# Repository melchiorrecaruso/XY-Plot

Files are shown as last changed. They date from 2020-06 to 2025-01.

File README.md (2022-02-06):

# **XY-Plot**

A plotter is a printer designed for printing vector graphics. Instead of printing individual dots on the paper, plotters draw continuous lines.
This makes plotters ideal for printing architectural blueprints, engineering designs, and other CAD drawings. 

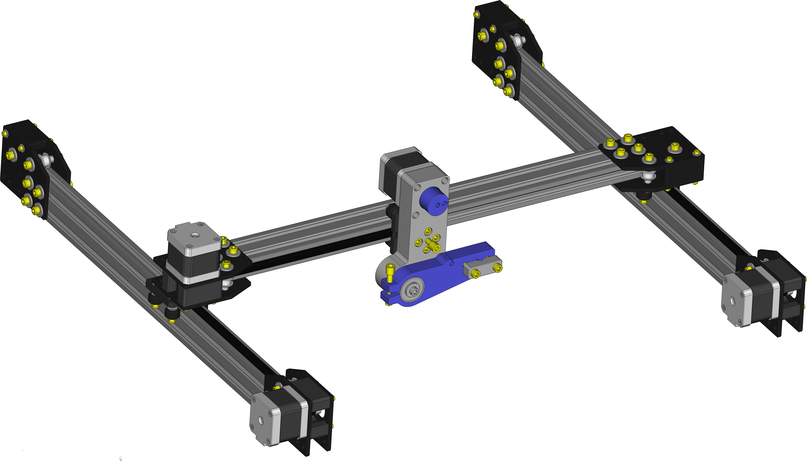
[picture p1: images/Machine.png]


## **XY-Plot hardware requirements**

The main components are:

>-  1x Arduino Uno R3 board or Mega 2560 R3;
>-  1x CNC Shield V3 expansion board;
>-  4x DRV8825 stepper motor driver;
>-  4x Stepper motor Nema-17 (min torque 40 Ncm);
>-  3x Timing belt pulley GT2 20T 5mmn bore;
>- 12x Smooth idler pulley with bearings GT2 20T 5mm bore;
>- 10m GT2 timming belt;
>-  1x 12V/5A power supplier;
>-  1x 3D-Printer for printing all hardware parts;
>-  40x40 beams, carriages. See [OpenBuilds parts store](https://openbuildspartstore.com/);
>-  Washers, bolts and nuts.

### **X Linear Actuator**
Prints parts and assembly two X axis linear actuator.

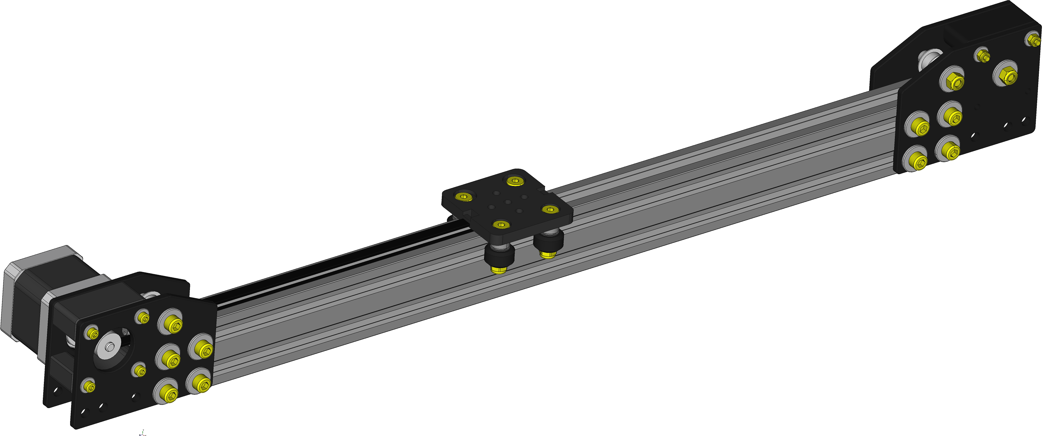
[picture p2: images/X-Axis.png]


### **Y Linear Actuator & Pen Holder**
Prints parts, assembly one Y axis linear actuator and pen holder.

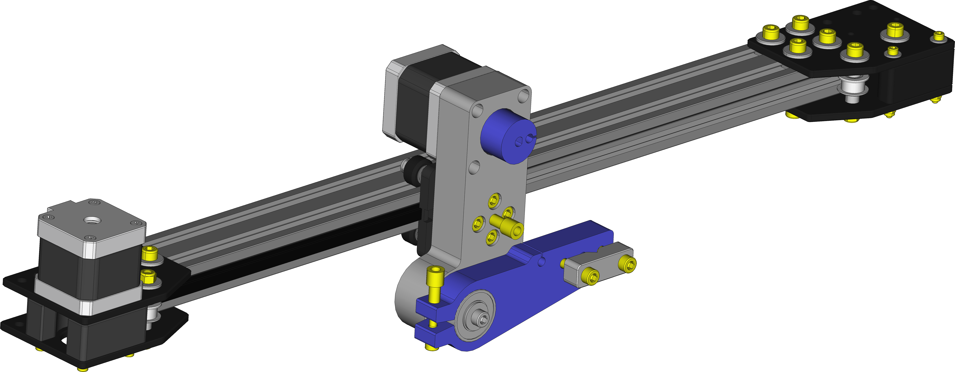
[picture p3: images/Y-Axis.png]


## **XY-Plot software requirements**

For compiling XY-Plot Client use [Lazarus IDE and FreePascal compiler](https://www.lazarus-ide.org/index.php?page=downloads).

**Libraries**:

>- [BGRA Controls Library](https://bgrabitmap.github.io/)
>- [LNet Library](https://lnet.wordpress.com/)

Use integrated [Online Package Manager](https://wiki.freepascal.org/Online_Package_Manager ) for installing all libraries.

**Build Client**:

```console
lazbuild --build-mode=Release xyplot.lpi
lazbuild --build-mode=Debug xyplot.lpi
```

**Build Server**:

For building and loading server sketch on Arduino board use [Arduino IDE](https://www.arduino.cc/en/Main/Software).

## **Before assembling**

Set the Vref current on DRV8825 stepper drivers. See the guide

>- [How to control a stepper motor with DRV8825](https://www.makerguides.com/drv8825-stepper-motor-driver-arduino-tutorial/)

## **Connecting to Arduino**

Nema 17 motors have 200 steps for rotation but by enabling microsteps on the Pololu drivers we can obtain up to 3200 steps for rotation which allows for much more precision. For doing that add four jumpers on green pins. 

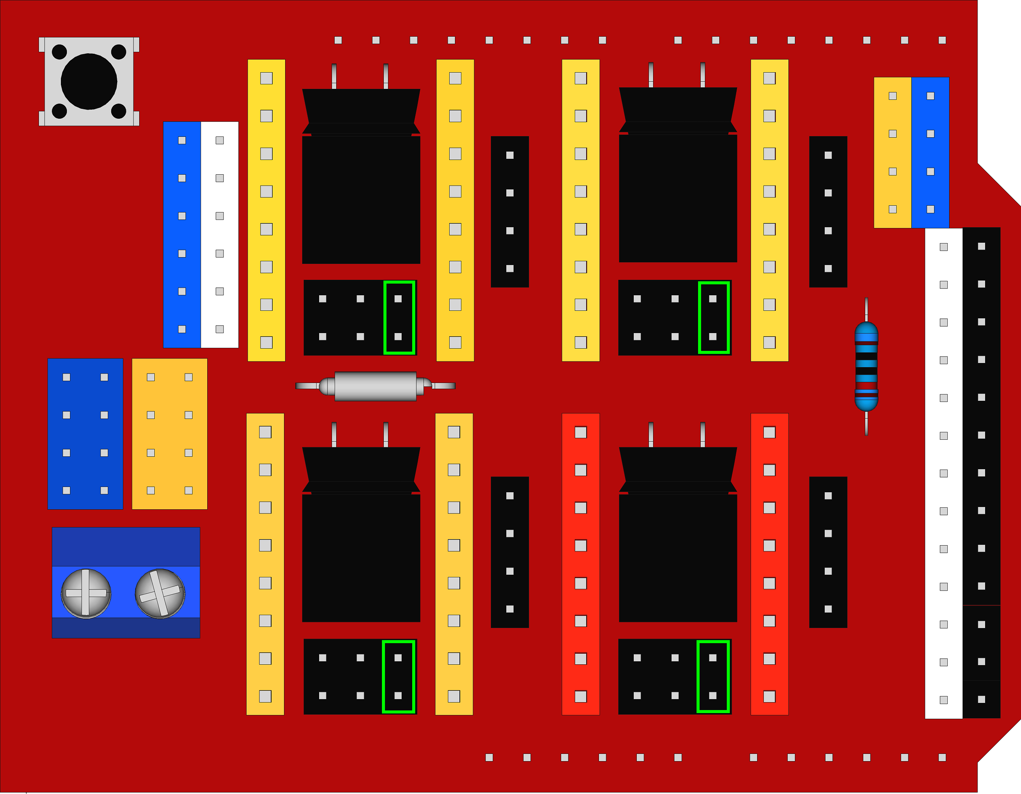
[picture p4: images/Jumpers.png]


**Then**
- Mount the stepper drivers on CNC schield board;
- Apply two jumpers on green pins for clonig X axis;
- Connect X motors to the blue pins;
- Connect Y motor to red pins;
- Connect Z motor to yellow pins.

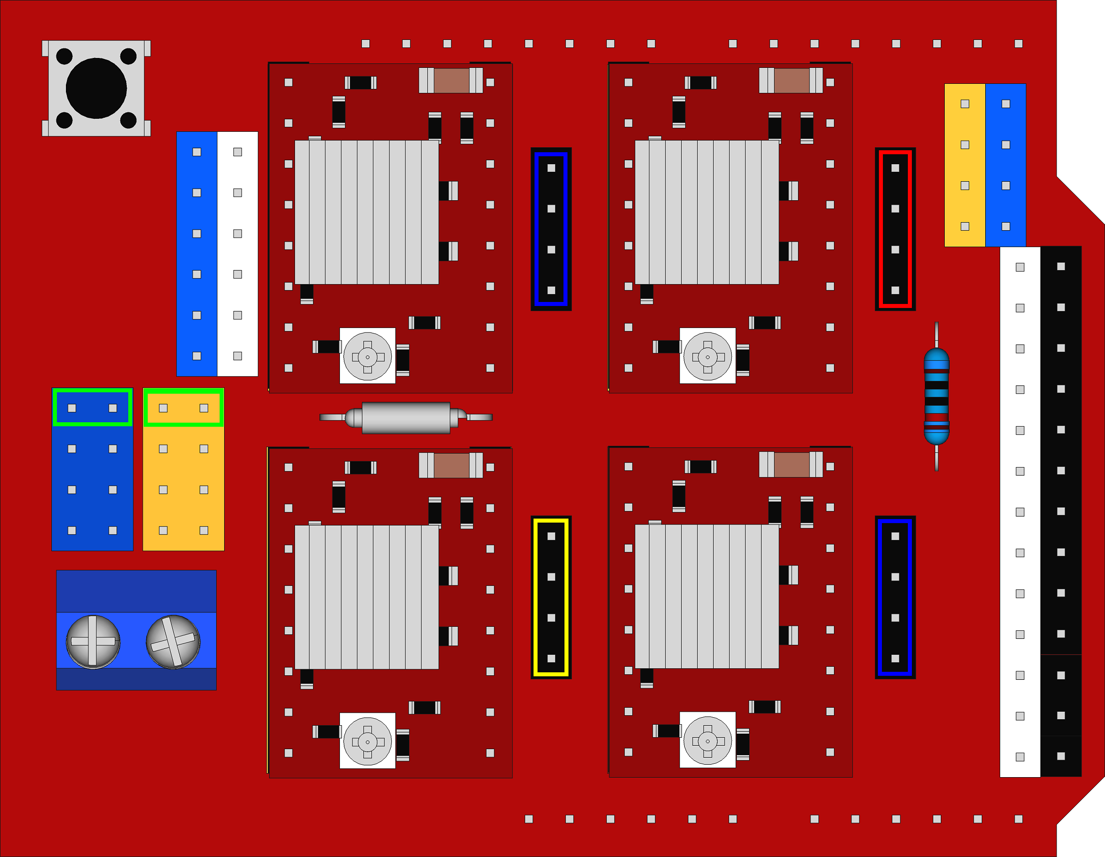
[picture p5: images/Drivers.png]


**Then**
- Mount CNC Shield on arduino board;
- Connect Arduino board to PC by usb port;
- Connect 12V power supply to CNC schield.

## **Starting**

Open XY-Plot client for connecting and controlling Plotter.

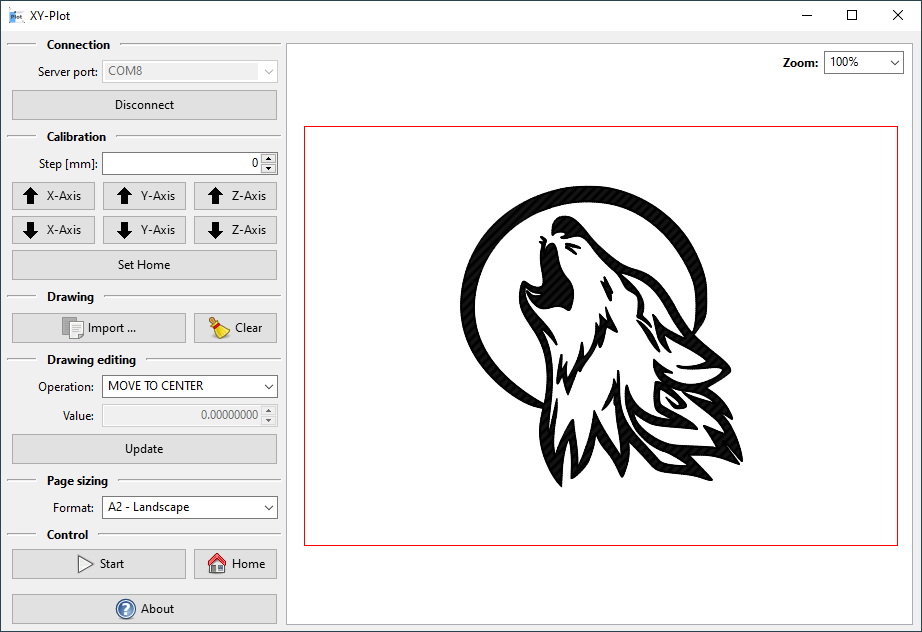
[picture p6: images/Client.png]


## **Boards Box**

Below a boards box example.

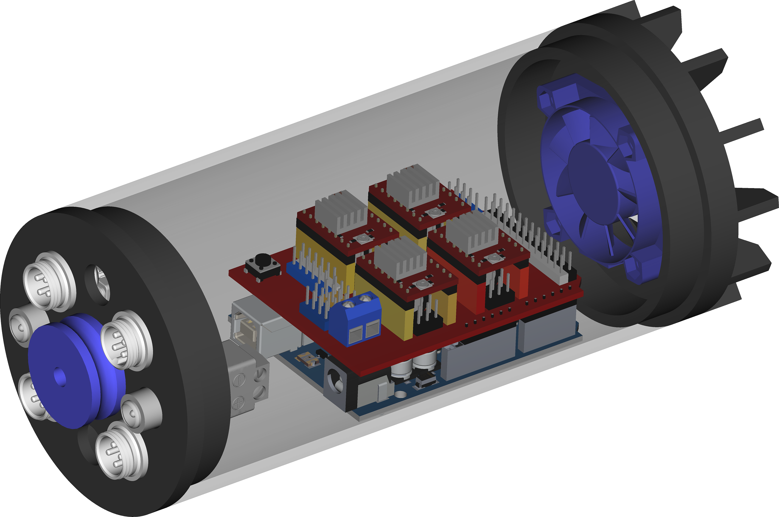
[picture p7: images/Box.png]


## **LICENSE**
[GNU General Public License v3.0](LICENSE)

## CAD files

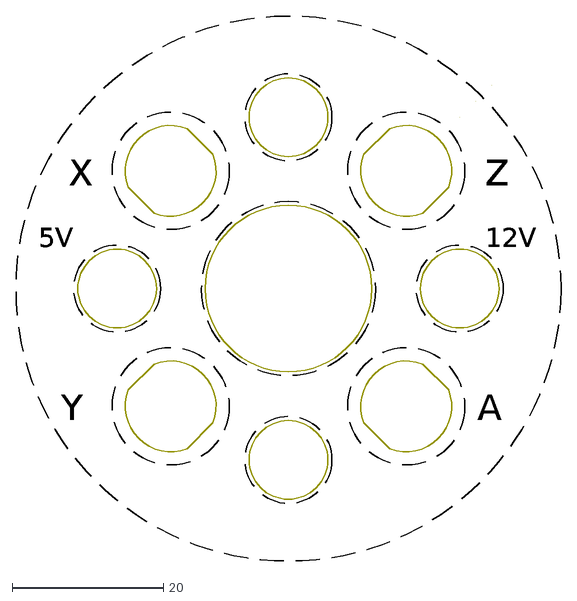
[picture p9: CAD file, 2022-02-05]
hardware/Decal/decal.dxf
X
Y
A
Z
12V
5V

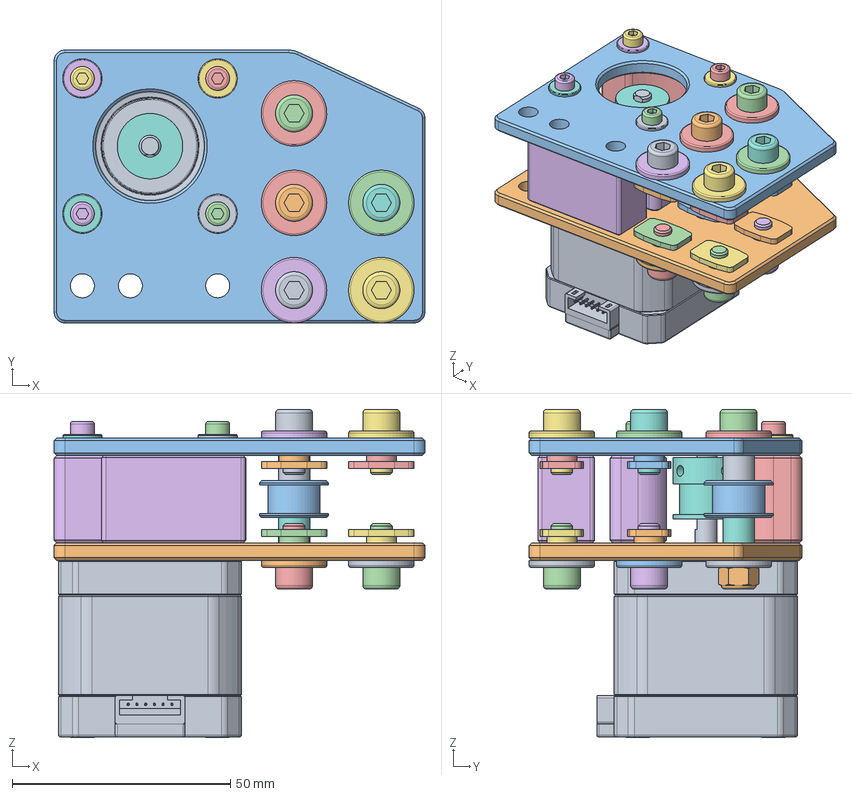
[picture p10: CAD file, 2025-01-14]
hardware/xyp1102.FCStd
85.0 x 62.5 x 75.3 mm
xyp1014_002
xyp1012_001
xyp1012_002
xyp1016_001
xyp1016_002
xyp1016_003
xyp1016_004
xyp1017_001
xyp1017_002
xyp1017_003
xyp1017_004
xyp1017_005
xyp1017_006
xyp1017_007
xyp1017_008
xyp1016_007
xyp1016_008
xyp1016_009
xyp1016_010
xyp1019_001
xyp1019_002
xyp1019_003
xyp1019_004
xyp1020_001
xyp1016_012
xyp1010_002
xyp1022_001
xyp1018_003
xyp1016_013
xyp1026_001
xyp1027_001
xyp1046_001
xyp1046_002
xyp1027_002
xyp1027_003
xyp1027_004
xyp1026_002
xyp1029_001
xyp1029_002
xyp1029_003
xyp1029_004
xyp1027_005
xyp1027_006
xyp1027_007
xyp1027_008
xyp1009_001

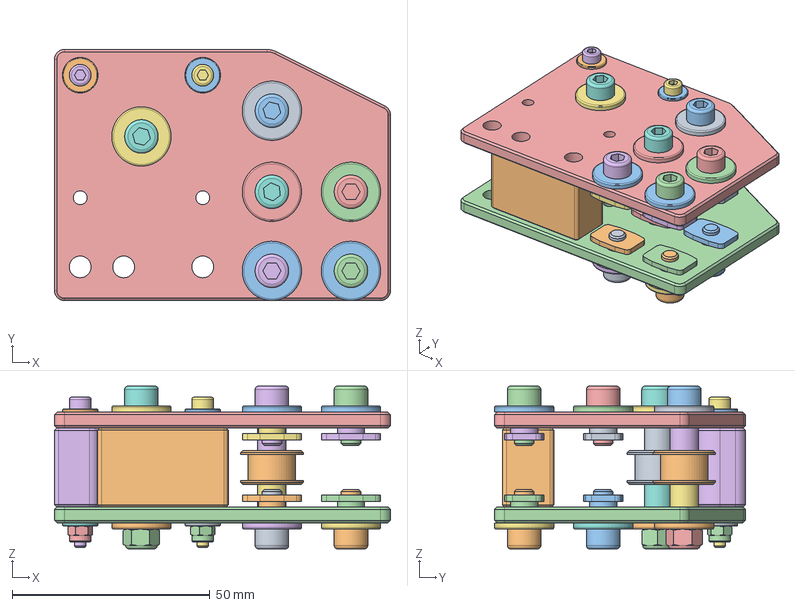
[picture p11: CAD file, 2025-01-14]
hardware/xyp1103.FCStd
85.0 x 63.5 x 41.2 mm
xyp1016_001
xyp1016_002
xyp1016_003
xyp1016_004
xyp1017_001
xyp1017_002
xyp1017_003
xyp1017_004
xyp1017_005
xyp1017_006
xyp1017_007
xyp1017_008
xyp1016_007
xyp1016_008
xyp1016_009
xyp1016_010
xyp1016_012
xyp1022_001
xyp1018_003
xyp1025_001
xyp1025_002
xyp1026_001
xyp1016_017
xyp1018_007
xyp1022_002
xyp1016_019
xyp1016_021
xyp1010_004
xyp1010_007
xyp1019_001
xyp1019_004
xyp1029_001
xyp1029_002
xyp1029_005
xyp1029_006
xyp1030_002
xyp1030_003
xyp1046_001
xyp1046_002
xyp1046_003
xyp1046_004
xyp1027_001
xyp1027_002
xyp1027_003
xyp1027_004
xyp1027_005
xyp1027_006
xyp1027_007
xyp1027_008
xyp1009_001

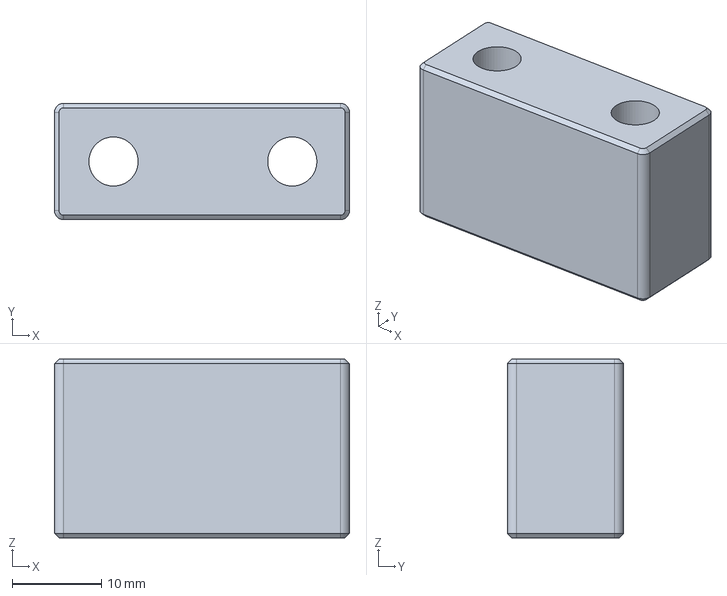
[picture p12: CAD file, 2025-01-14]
hardware/xyp1009.FCStd
33.0 x 13.0 x 20.0 mm

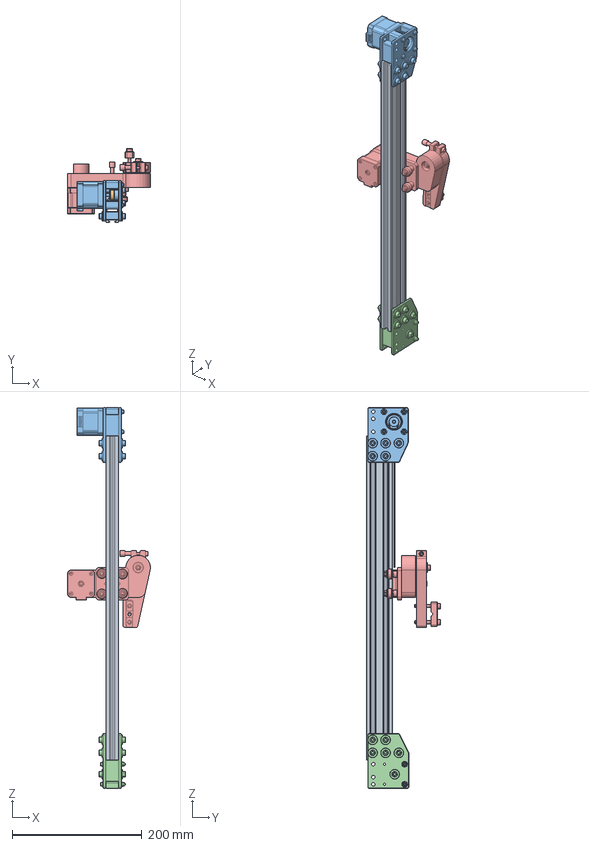
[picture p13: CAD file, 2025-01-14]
hardware/xyp1100.FCStd
128.0 x 114.3 x 588.0 mm
xyp1000_001
xyp1021_001
xyp1102_001
xyp1103_001
xyp1104B_001

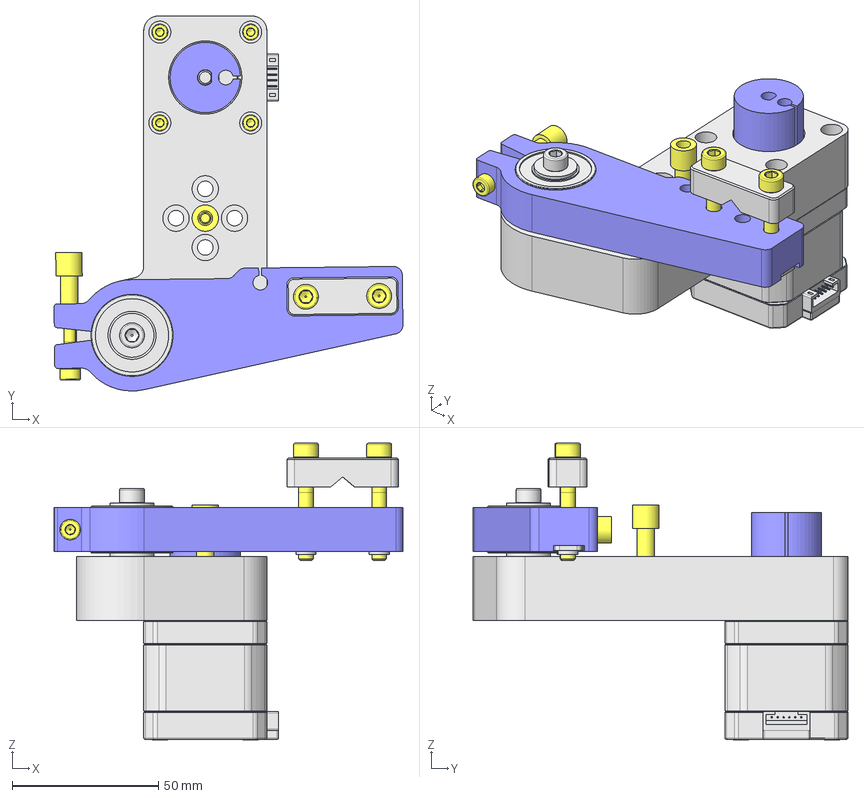
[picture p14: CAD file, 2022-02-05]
hardware/xyp1107B.FCStd
119.1 x 128.0 x 101.3 mm
xyp1062_001
xyp1014_001
xyp1063_001
xyp1059_001
xyp1064_001
xyp1105_001
M4x30-Screw
M3x10-Screw
M3x10-Screw100
M3x10-Screw101
M3x10-Screw102
xyp1064_002
M4x30-Screw001
xyp1040_001
M5x35-Screw
M5x35-Screw001
xyp1027_001
xyp1027_002

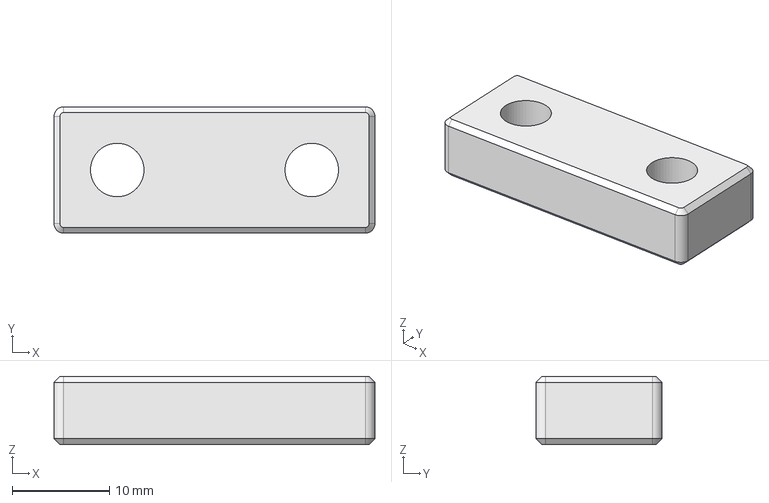
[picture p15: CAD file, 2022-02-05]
hardware/xyp1039.FCStd
33.0 x 13.0 x 7.00 mm

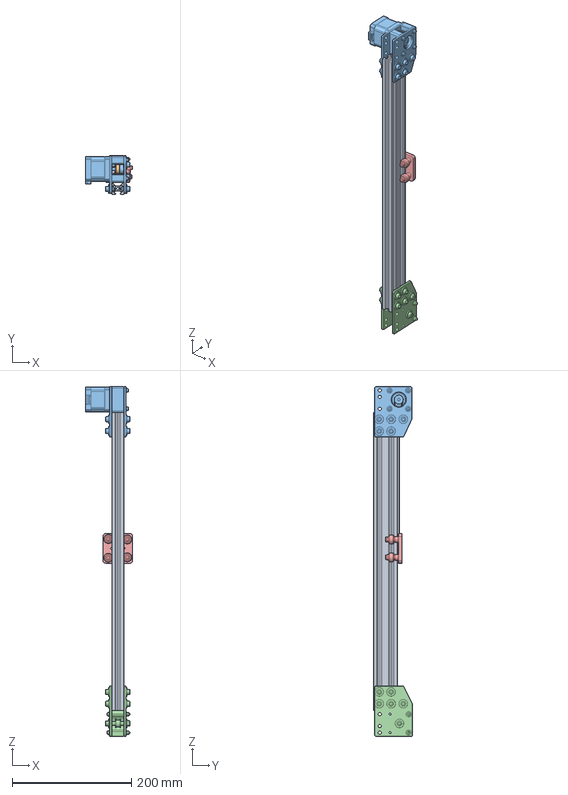
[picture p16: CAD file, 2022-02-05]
hardware/xyp1106.FCStd
79.7 x 65.5 x 588.0 mm
xyp1000_001
xyp1021_001
xyp1102_001
xyp1103_001
xyp1101_001

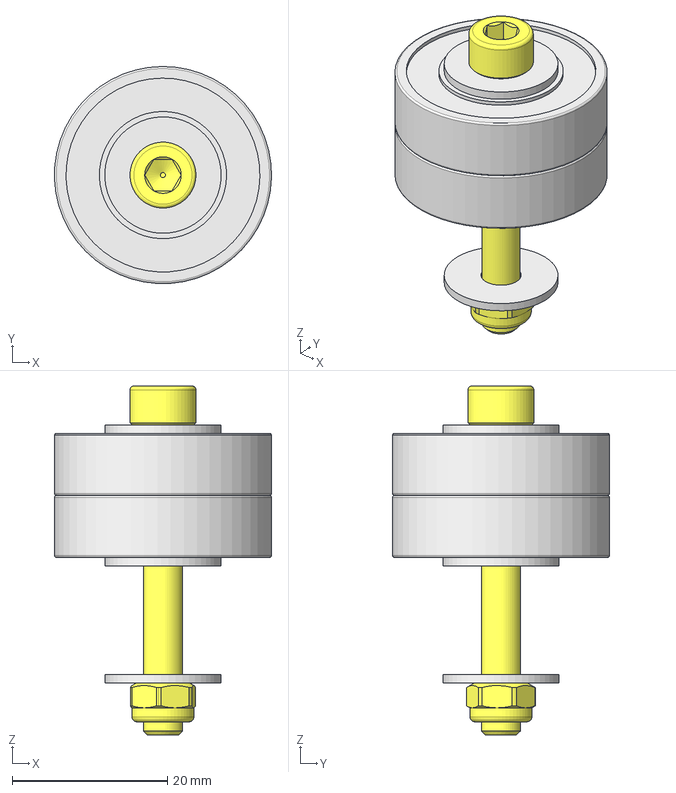
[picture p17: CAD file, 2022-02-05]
hardware/xyp1105.FCStd
28.0 x 28.0 x 45.0 mm
xyp1036_001
xyp1036_002
xyp1035_001
xyp1035_002
M5x40-Screw
M5-Nut
M5-Washer
M5-Washer077
M5-Washer078

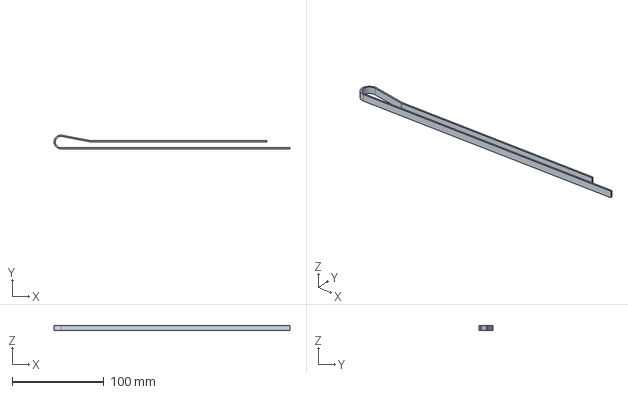
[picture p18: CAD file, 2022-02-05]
hardware/xyp1021.FCStd
257.5 x 15.1 x 6.00 mm

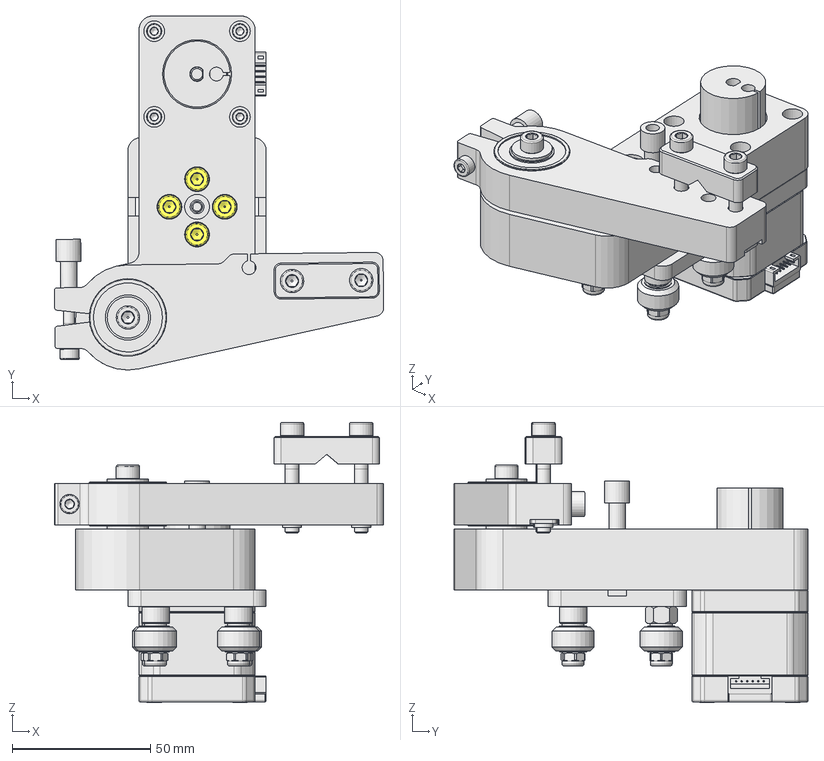
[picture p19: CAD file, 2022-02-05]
hardware/xyp1104B.FCStd
119.1 x 128.0 x 101.3 mm
xyp1101_001
xyp1107B_001
M5x20-Screw
M5x20-Screw020
M5x20-Screw021
M5x20-Screw022

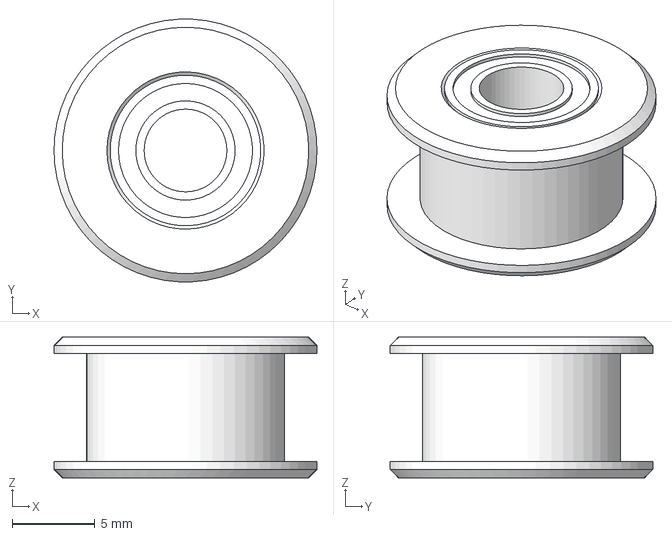
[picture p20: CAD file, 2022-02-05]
hardware/xyp1022.FCStd
15.9 x 15.9 x 8.50 mm

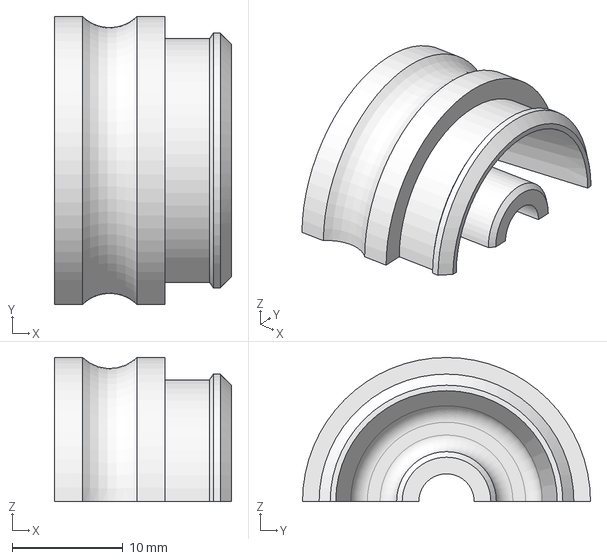
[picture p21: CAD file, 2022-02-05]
hardware/xyp1079.FCStd
16.0 x 26.0 x 13.0 mm

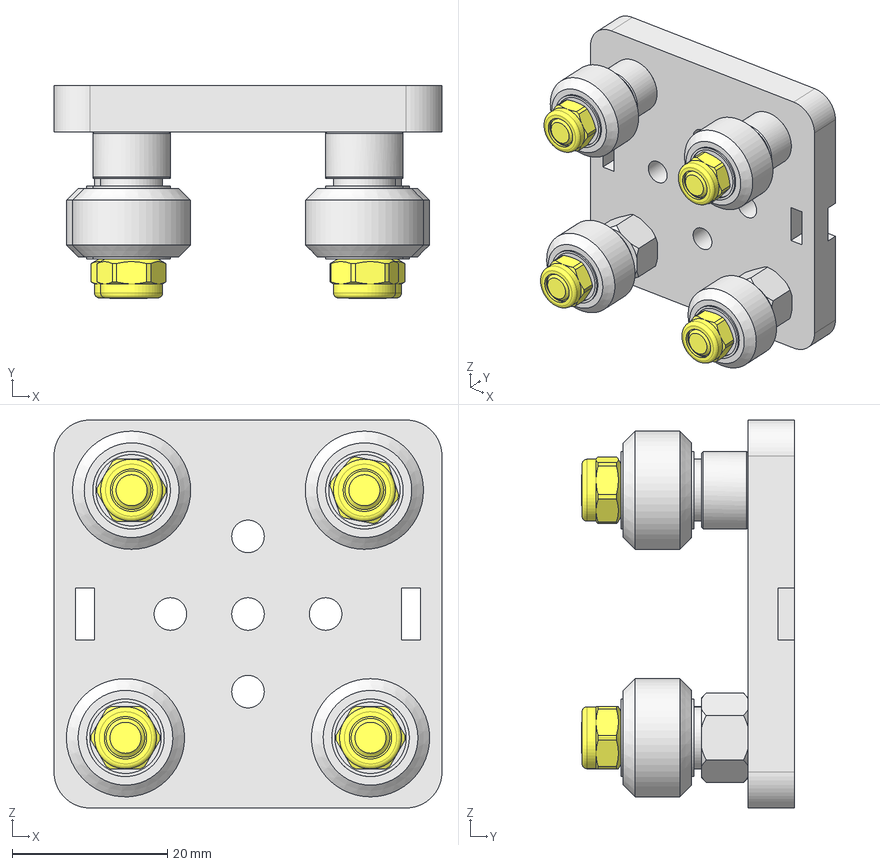
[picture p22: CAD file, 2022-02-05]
hardware/xyp1101.FCStd
50.0 x 27.5 x 50.0 mm
xyp1007_001
xyp1003_001
xyp1003_002
xyp1002_001
xyp1002_002
xyp1009_001
xyp1009_002
xyp1009_003
xyp1009_004
xyp1006_001
xyp1006_002
xyp1006_003
xyp1006_004
xyp1001_001
xyp1001_002
xyp1001_003
xyp1001_004
M5-Nut
M5-Nut001
M5-Nut002
M5-Nut003

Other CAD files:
hardware/xyp1000.FCStd
hardware/xyp1070.FCStd
hardware/xyp1073A.FCStd
hardware/xyp1078A.FCStd
hardware/GrabCAD/ARDUINO-UNO-R3.FCStd
hardware/GrabCAD/CNC-ShieldV3.FCStd
hardware/GrabCAD/DC-PowerAdapter.FCStd
hardware/GrabCAD/FAN-40x40.FCStd
hardware/GrabCAD/GX12-4PIN.FCStd
hardware/STL/xyp1009.stl
hardware/STL/xyp1012.stl
hardware/STL/xyp1025.stl
hardware/STL/xyp1026.stl
hardware/STL/xyp1039.stl
hardware/STL/xyp1040.stl
hardware/STL/xyp1059.stl
hardware/STL/xyp1062.stl
hardware/STL/xyp1063.stl
hardware/STL/xyp1069.stl
hardware/STL/xyp1070.stl
hardware/STL/xyp1071.stl
hardware/STL/xyp1072.stl
hardware/STL/xyp1079.stl
hardware/xyp1001.FCStd
hardware/xyp1002.FCStd
hardware/xyp1003.FCStd
hardware/xyp1004.FCStd
hardware/xyp1006.FCStd
hardware/xyp1007.FCStd
hardware/xyp1012.FCStd
hardware/xyp1014.FCStd
hardware/xyp1020.FCStd
hardware/xyp1025.FCStd
hardware/xyp1026.FCStd
hardware/xyp1027.FCStd
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

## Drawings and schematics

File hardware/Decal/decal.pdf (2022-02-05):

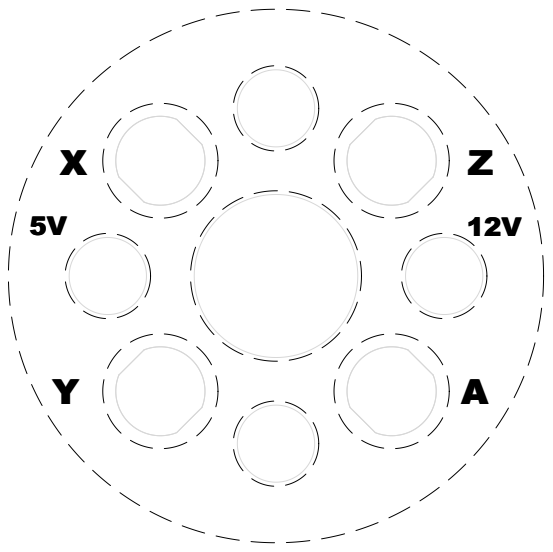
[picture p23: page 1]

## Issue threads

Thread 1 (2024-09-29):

STL files for printing

krispatl, 2024-09-29:
Where can i find the STL files for printing?

Thanks

melchiorrecaruso, 2025-01-09:
Sorry, I just see your message.
Inside the hardware folder you will find all the 3D models. You will need FreeCad to open them and convert them to STL. If you are still interested I can do it for you.

krispatl, 2025-01-13:
Hi!
It would be great if you could assist me with the stl files! I have all of
the parts as outlined in your git repo. I have upgraded the steppers to a
higher torque model.

Thank you!

Kris

On Thu, Jan 9, 2025 at 4:12 PM Melchiorre Caruso ***@***.***>
wrote:

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

--
*Kris Pilcher*

www.KrisPilcher.com
***@***.***
https://www.instagram.com/krispatl/
(678)949-2849

melchiorrecaruso, 2025-01-14:
Hi Kris,

you can find the STL files for the parts to be printed inside folder /hardware/STL.
You'll still need FreeCAD at least to view the assembly files (named as 11xx.FCStd)
and figure out what else you need to complete the assembly.

If you still need help, I'll be glad to assist you.

Warm regards
Melchiorre

Closed 2025-05-30.

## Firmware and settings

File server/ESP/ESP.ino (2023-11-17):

// XY-Plotter Server for ESP32/ESP8266 board

// Author: Melchiorre Caruso
// Date:   03 Apr 2021

// Serial data format:
//
// bit0 -> increase internal main-loop time
// bit1 -> decrease internal main-loop time
// bit2 -> x-motor stp ()
// bit3 -> y-motor stp ()
// bit4 -> z-motor stp ()
// bit5 -> x-motor dir ()
// bit6 -> y-motor dir ()
// bit7 -> z-motor dir ()

#define _TIMERINTERRUPT_LOGLEVEL_  0

#include <math.h>
#if defined(ESP32) 
  #include "ESP32Module.h" 
  #include "ESP32TimerInterrupt.h"
#endif
#if defined(ESP8266)
  #include "ESP8266Module.h"  
  #include "ESP8266TimerInterrupt.h"
#endif

uint8_t Buffer[256];
uint8_t BufferIndex   = 0;
uint8_t BufferSize    = 0; 
volatile uint8_t Bits = 0; 

#define NumOfPoints     0x80000000 
#define SpeedTableSize  201
volatile bool     Flag  = false;   
volatile uint32_t Accum = 0;
volatile uint32_t SpeedIndex = 0;
         uint32_t SpeedTable[SpeedTableSize];

char ssid[] = "QUACK-NET";
char pass[] = "0SVDTPGPQVGOVO7HN";

WiFiClient client1;
WiFiServer server1(8888);

#if defined(ESP32) 
  ESP32Timer timer1(1);
#endif  
#if defined(ESP8266)
  ESP8266Timer timer1;
#endif

#if defined(ESP32)  
  bool IRAM_ATTR onTime1(void * TimerNo) {
#endif 
#if defined(ESP8266) 
  void IRAM_ATTR onTime1() { 
#endif
  Accum += SpeedTable[SpeedIndex];
  if (Accum > NumOfPoints) { 
    if (Flag == true) {  
      digitalWrite(MOTOR_X_DIR, bitRead(Bits, 5));
      digitalWrite(MOTOR_Y_DIR, bitRead(Bits, 6));
      digitalWrite(MOTOR_Z_DIR, bitRead(Bits, 7));        
      digitalWrite(MOTOR_X_STP, bitRead(Bits, 2));
      digitalWrite(MOTOR_Y_STP, bitRead(Bits, 3));   
      digitalWrite(MOTOR_Z_STP, bitRead(Bits, 4)); 
      if (bitRead(Bits, 0)) { SpeedIndex++; }        
      if (bitRead(Bits, 1)) { SpeedIndex--; }  

        if (SpeedIndex > 200)  { Serial.println(SpeedIndex); }     
        if (SpeedIndex <   0)  { Serial.println(SpeedIndex); }     
      
      Bits = 0;   
      Flag = false;     
    } else {
      digitalWrite(MOTOR_X_STP, LOW);        
      digitalWrite(MOTOR_Y_STP, LOW);   
      digitalWrite(MOTOR_Z_STP, LOW);
      Flag = true;
    }      
    Accum -= NumOfPoints;                          
  }
  
  #if defined(ESP32)  
    return true;  
  #endif  
}
 
void setup() {
  Serial.begin(115200);
  // init wifi
  WiFi.begin(ssid, pass);
  // disable stepper motors
  pinMode(MOTOR_OFF, OUTPUT);
  digitalWrite(MOTOR_OFF, HIGH);
  // init stepper X/Y/Z
  pinMode(MOTOR_X_STP, OUTPUT);
  pinMode(MOTOR_Y_STP, OUTPUT);
  pinMode(MOTOR_Z_STP, OUTPUT);
  pinMode(MOTOR_X_DIR, OUTPUT);
  pinMode(MOTOR_Y_DIR, OUTPUT);
  pinMode(MOTOR_Z_DIR, OUTPUT);   
  // init server
  server1.begin();     
  // enable stepper motors
  digitalWrite(MOTOR_OFF, LOW);    
  // init speed table
  double Freq     = 1000.00;  // Hz
  double CoreFreq = 16000.00; // Hz
  double KC       = 2*(Freq/CoreFreq*(double)NumOfPoints)/(sqrt(2)-sqrt(1));  
  for (uint16_t i = 1; i <= SpeedTableSize; i++) { 
    SpeedTable[SpeedTableSize - i] = trunc(KC*(sqrt(i + 1)-sqrt(i)));     
  }     
  // connect to WiFi
  while (WiFi.status() != WL_CONNECTED) { delay(50); }
  // init interrupt
  timer1.attachInterrupt(CoreFreq, onTime1);    
}

void loop() { 

   if (Bits == 0) {      
    if (BufferIndex < BufferSize) {        
      Bits = Buffer[BufferIndex];
      BufferIndex++;      
    }
    if (BufferIndex == BufferSize) {
      if (client1) {
        if (client1.connected()) {            
          BufferIndex = 0;  
          BufferSize  = min(128, client1.available());         
          if (BufferSize > 0)  {                                 
            client1.read(Buffer, BufferSize);
            client1.write(BufferSize);               
          }          
        } else { client1.stop(); } 
      } else { 
        client1 = server1.available();
      } 
    }
  }  

}

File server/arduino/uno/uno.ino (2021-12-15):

// XY-Plotter Server for Arduino Uno

// Author: Melchiorre Caruso
// Date:  15 Dec 2021

// Serial data format

// bit0 -> decrease internal main-loop time
// bit1 -> increase internal main-loop time
// bit2 -> x-motor stp (avr register PORTD2)
// bit3 -> y-motor stp (avr register PORTD3)
// bit4 -> z-motor stp (avr register PORTD4)
// bit5 -> x-motor dir (avr register PORTD5)
// bit6 -> y-motor dir (avr register PORTD6)
// bit7 -> z-motor dir (avr register PORTD7)

#include <math.h>

uint8_t Bits = 0; 
uint8_t Buffer[255];
uint8_t BufferIndex = 0;
uint8_t BufferSize = 0;

uint32_t LoopStart = micros();
uint32_t LoopNow   = 0;
uint32_t LoopDelay = 440;

uint32_t RampKB = 40000;
uint16_t RampIndex = 1;

void setup() {
  // init serial
  Serial.begin(115200); 
  while (Serial.available() > 0) { Serial.read(); } 
  // disable stepper motors
  DDRB |= B00000001; 
  PORTB |= B00000001; 
  // init stepper X/Y/Z
  DDRD |= B11111100;
  // enable stepper motors   
  PORTB &= B11111110;
}

void loop() {

  LoopNow = micros();
  if ((unsigned long)(LoopNow - LoopStart) >= LoopDelay) {
    // SET X-DIR, Y-DIR and Z-DIR PIN,   
    // SET LOW X-STEP, Y-STEP and Z-STEP PIN
    PORTD = (PORTD & B00000011) | (Bits & B11100000);             
    // SET HIGH X-STEP, Y-STEP and Z-STEP PIN
    PORTD = (PORTD & B11100011) | (Bits & B00011100);
                   
    if (Bits & B00000001) { RampIndex++; }     
    if (Bits & B00000010) { RampIndex--; }        
 
    if (BufferIndex < BufferSize) {
      Bits = Buffer[BufferIndex];
      BufferIndex++;             
    } else { 
      Bits = 0; 
    }    
    LoopStart = LoopNow;
    LoopDelay = round(RampKB * (sqrt(RampIndex + 1)-sqrt(RampIndex)));  
  }  

  if (BufferIndex == BufferSize) {         
    BufferIndex = 0;  
    BufferSize  = Serial.available();   
    if (BufferSize > 0) {                                 
      Serial.readBytes(Buffer, BufferSize);
      Serial.write(BufferSize);   
    }         
  }
}

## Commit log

2020-06-07 First upload
    [ramps.ods]
2020-06-07 Upload hardware files
    [xyp1000.FCStd, xyp1001.FCStd, xyp1002.FCStd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]
2020-07-22 New version 1.2
    [ramps.ods, xyp1040.FCStd, xyp1041.FCStd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]
2020-12-22 Deleted servo routines
2021-01-20 updated hardware
    [xyp1005.FCStd, xyp1008.FCStd, xyp1010.FCStd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]
2021-01-20 Update wiring
2021-02-14 Update hardware
    [xyp1073A.FCStd, xyp1078.FCStd, xyp1078A.FCStd]
2021-02-14 Added CRC8 routine
    [wiring.dxf]
2021-02-14 v1.4 alpha Release
    [CNC-ShieldV3.FCStd, DC-PowerAdapter.FCStd, FAN40x40.FCStd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]
2021-02-28 Update driver resolution
2021-03-16 Some serial bugfix
    [ramps.ods, xyp1079.FCStd]
2021-05-16 Bugfix
    Cleaning and bugfix 2
    [uno.ino]
2021-06-13 New FIT feature and bugfixes
    [uno.ino]
2021-08-07 hardware upgrades
    [FAN40x40.FCStd, NodeMCU8266.FCStd, xyp1100.FCStd]
2021-12-15 New version 1.6
    [ramps.ods]
2022-02-05 New release
    [ARDUINO-UNO-R3.FCStd, CNC-ShieldV3.FCStd, DC-PowerAdapter.FCStd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]
2025-01-14 Updating spacer 1009 and assembly
    [xyp1009.FCStd, xyp1100.FCStd, xyp1102.FCStd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]
2025-01-14 Adding STL models
    [xyp1009.stl, xyp1012.stl, xyp1025.stl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]
